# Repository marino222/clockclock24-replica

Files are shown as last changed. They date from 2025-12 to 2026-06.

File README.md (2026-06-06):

# ClockClock 24 Replica

This project is a hardware and software replica of the kinetic art piece "ClockClock 24" by *Humans Since 1982*, inspired by and building upon the work of [Vallasc](https://github.com/Vallasc/clockclock24-replica) with several hardware modifications and improvements. The clock features 24 double-shaft stepper motors arranged in an 8x3 matrix, with motors grouped in sets of three on custom PCBs, of which there are eight in total. Each board is controlled by a Raspberry Pi Pico microcontroller acting as a slave, while all slave boards communicate with a central ESP32 master via the I2C protocol. The ESP32 also provides a web interface for remote control and configuration.

chaos_intro

---

## Table of Contents

1. [Repository Structure](#repository-structure)
2. [Hardware](#hardware)
    1. [Electronics](#electronics)
        1. [Motors](#motors)
        2. [Motor Drivers](#motor-drivers)
        3. [Microcontrollers](#microcontrollers)
        4. [PCB](#pcbs)
        5. [Power Supply](#power-supply)
    2. [Mechanics](#mechanics)
        1. [Clock hands](#clock-hands)
        2. [Fixation brackets](#fixation-brackets)
        3. [Front panel](#front-panel)
    3. [BOM](#bom)
3. [Software](#software)
    1. [Master](#master)
    2. [Slave](#slave)
    3. [Web Interface](#web-interface)
4. [Credits](#credits)

---

## Repository Structure

```
ClockClock 24 Replica/
├── 3D files/
│   ├── final/
│   └── test/
├── docs/
│   ├── datasheets/
│   └── images/
├── firmware/
│   ├── arduino/
│   │   ├── AdvancedBoardTest/
│   │   ├── BoardTest/
|   |   ├── SerialBoardTest/
│   │   └── SpeedoDriveTest/
│   ├── platformio/
│   │   ├── master/
│   │   └── slave/
│   └── README.md
├── pcb/
│   ├── Clock PCB/
│   └── Motor Driver/
└── README.md
```

---

## Hardware

### Electronics

#### Motors
To drive the clock hands, the BKA30D-R5 (equivalent to VID28-05) stepper motors were chosen. They have a total of 4 coils, allowing for two concentric drive shafts which makes them perfect for this application. These motors were originally designed for dashboard applications in the automotive industry. There are a number of other options with concentric shafts, but this one seemed to be most suitable as other similar projects also used it. Furthermore, it is cheaply available (around 4$ on Aliexpress) and draws little current.

<p align="center">
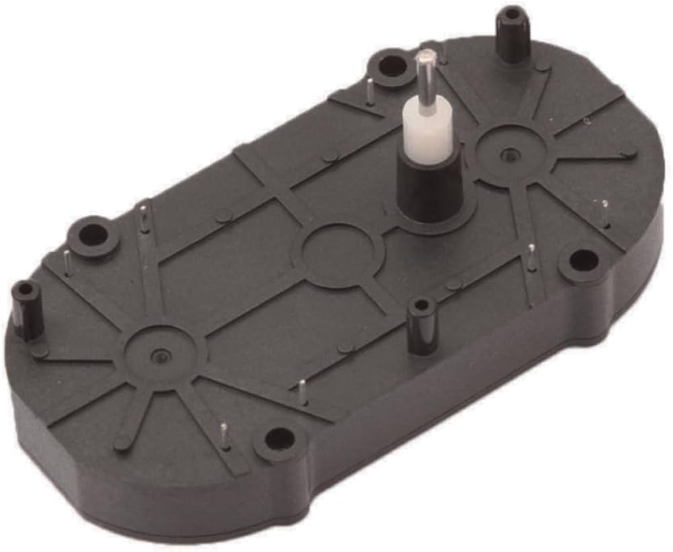
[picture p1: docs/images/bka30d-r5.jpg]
BKA30D-R5 stepper motor
    
    <br><em>BKA30D-R5 stepper motor</em>
</p>

The BKA30D-R5 allows for microstepping up to 1/12 degrees per microstep, which is ideal to achieve smooth movement of the clock hands. See datasheet for more details: [BKA30D-R5 Datasheet](docs/datasheets/BKA30D-xx_datasheet.pdf).

*Note: As standard, this motor comes with mechanical endstops. On Aliexpress there are some vendors that sell it without endstops, otherwise you will need to cut off the endstops yourself.*

---

#### Motor Drivers
The steppers could in theory be driven directly from the microcontroller. However, the GPIO pins are limited and it is usually best practice to use a dedicated motor driver. For this reason, the VID6606 motor driver was chosen. It is specifically designed for the BKA30D-R5 (VID28-05) motor. One VID6606 can drive 4 motors (8 coils) in total. Per motor, it only needs two inputs: `f(SCX)` and `DIR`. As standard, this controller has built-in microstepping, which means with each rising edge of the SCX input the motor will perform one microstep in the direction specified by the DIR input.

The [VID6606 Datasheet](docs/datasheets/VID6606_datasheet.pdf) specifically recommends the use of smoothing capacitors to reduce electrical noise. Therefore, this [Motor-Controller-PCB from Hackaday](https://hackaday.io/project/187630-stepper-driver-for-dashpanel-instruments) was used. I didn't make any changes to it because it was already tested by [doctek](https://hackaday.io/doctek). Thus, it is designed to be used as a breakout board on the custom Clock PCB.

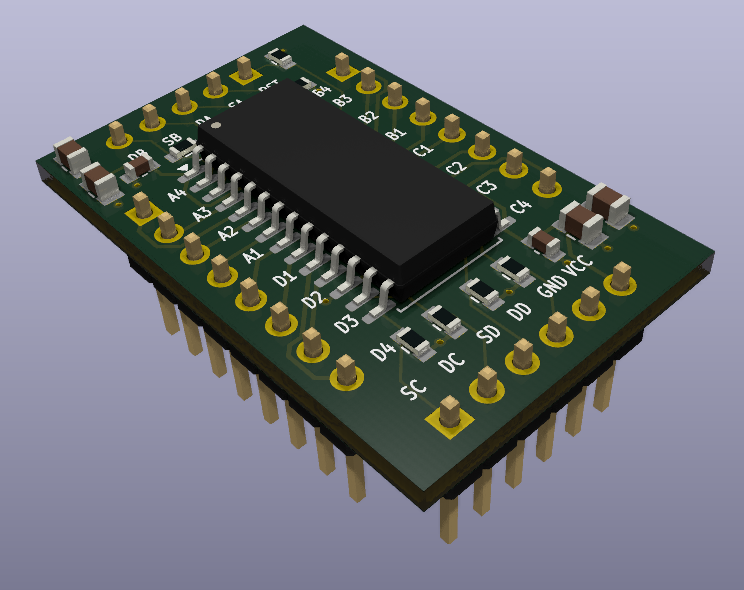
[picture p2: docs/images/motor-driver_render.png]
Rendered Motor Driver PCB

<p align="center"><em>Rendered image of the motor driver PCB</em></p>

During testing, the steppers were quite noisy. I first suspected the motor drivers and tried some alternatives (DRV8834, TMC2208), but that didn't help much, so I stayed with the VID6606. 

The real cause turned out to be mechanical play in the motor shafts. I also noticed the noise only appears at certain speeds, at full speed it mostly goes away. So adjusting the acceleration profile in software might help. For now I decided to leave the mechanical play as-is, since adding a bearing would be quite complex.

---

#### Microcontrollers
An ESP32 was chosen to run the master code, while multiple Raspberry Pi Picos are used as slave controllers. The ESP32 sends all the commands via I2C protocol to the slave boards. The main reason for this choice is that almost the same controllers were used in the reference project ([Vallasc/clockclock24-replica](https://github.com/Vallasc/clockclock24-replica)). Since I want to copy the software as closely as possible, I stuck with the same controllers. They are also widely available for a reasonable price and are easy to work with.

<p align="center">
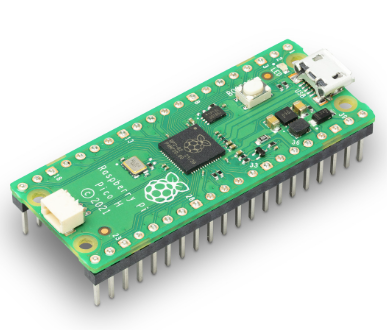
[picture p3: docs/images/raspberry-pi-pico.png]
Raspberry Pi Pico
    
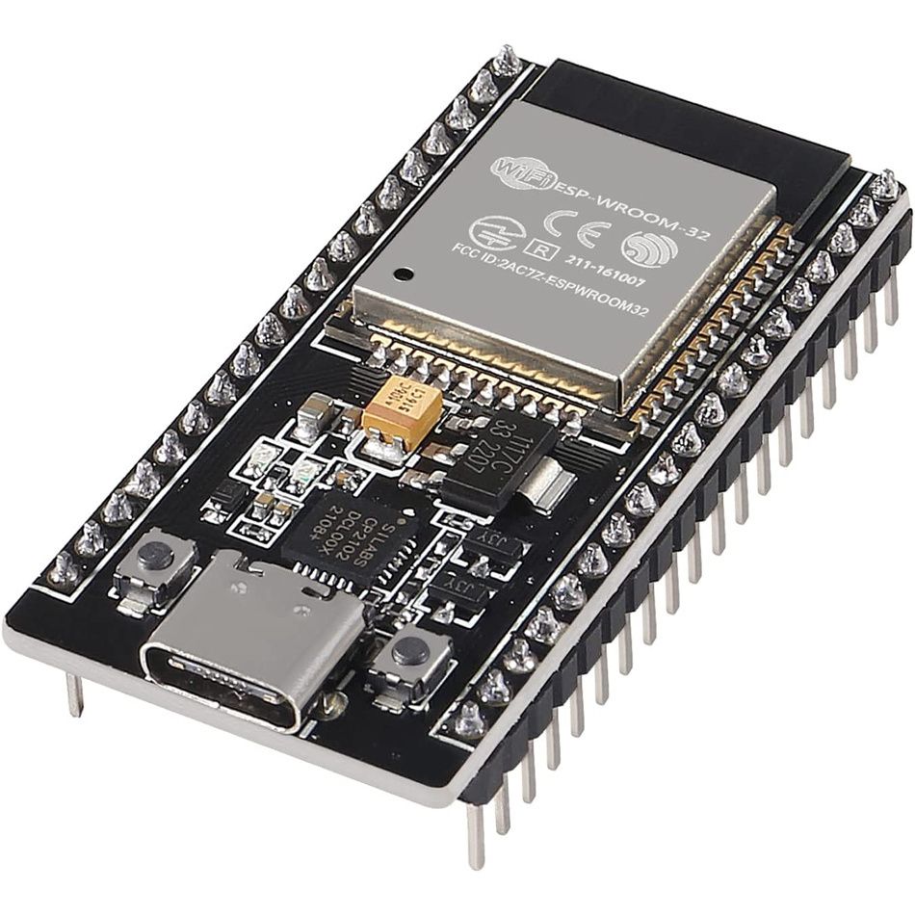
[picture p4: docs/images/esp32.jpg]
ESP32
    
</p>
<p align="center"><em>Raspberry Pi Pico (left) and ESP32 (right)</em></p>

---

#### PCB
For the project, a custom Clock PCB was designed to hold three BKA30D-R5 motors, which is the maximum number of motors that can be driven by one Raspberry Pi Pico regarding available GPIO pins. In total, there are eight of these PCBs, resulting in an 8x3 matrix of 24 motors. Each Clock PCB has two VID6606 motor driver breakout boards, of which one output is unused.

As a design choice, the PCB uses header pins to connect the motor drivers and the microcontroller. This makes it easy to replace components in case they break. While testing, this happened multiple times. Since the motor controllers were directly soldered onto the PCB in the beginning, I ended up throwing away the whole PCB each time a motor driver broke. The header pins solve this problem. As a bonus, the Picos can be switched out easily. This proved useful to quickly run a test program by replacing the "normal" slave controller with a test controller running different firmware.

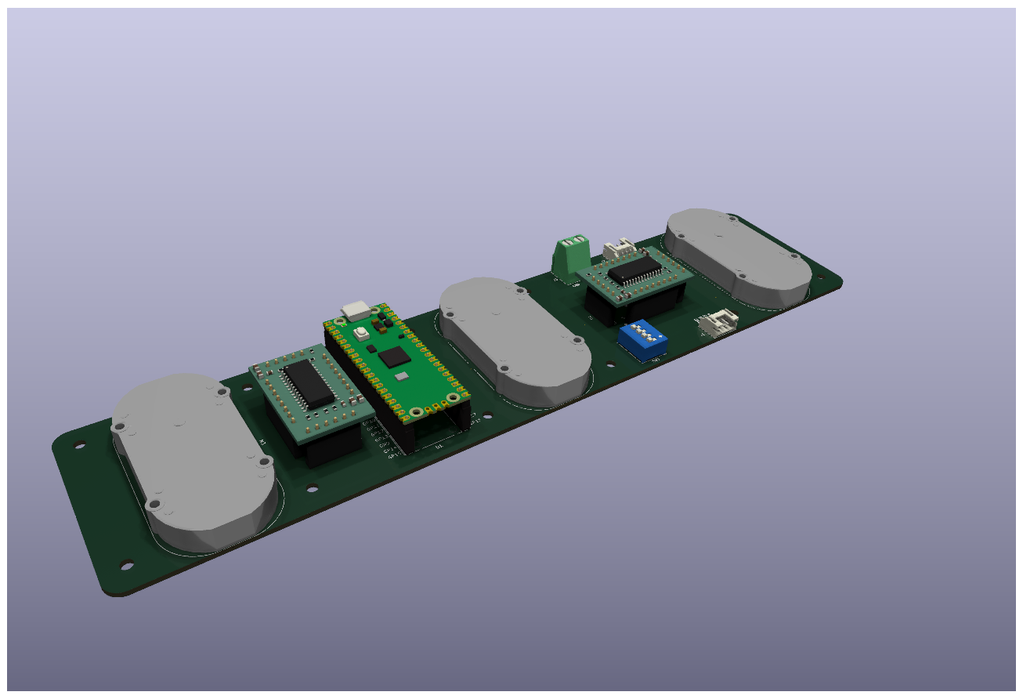
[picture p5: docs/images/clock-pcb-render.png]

<p align="center"><em>Rendered image of the Clock PCB. See PCB directory for more info</em></p>

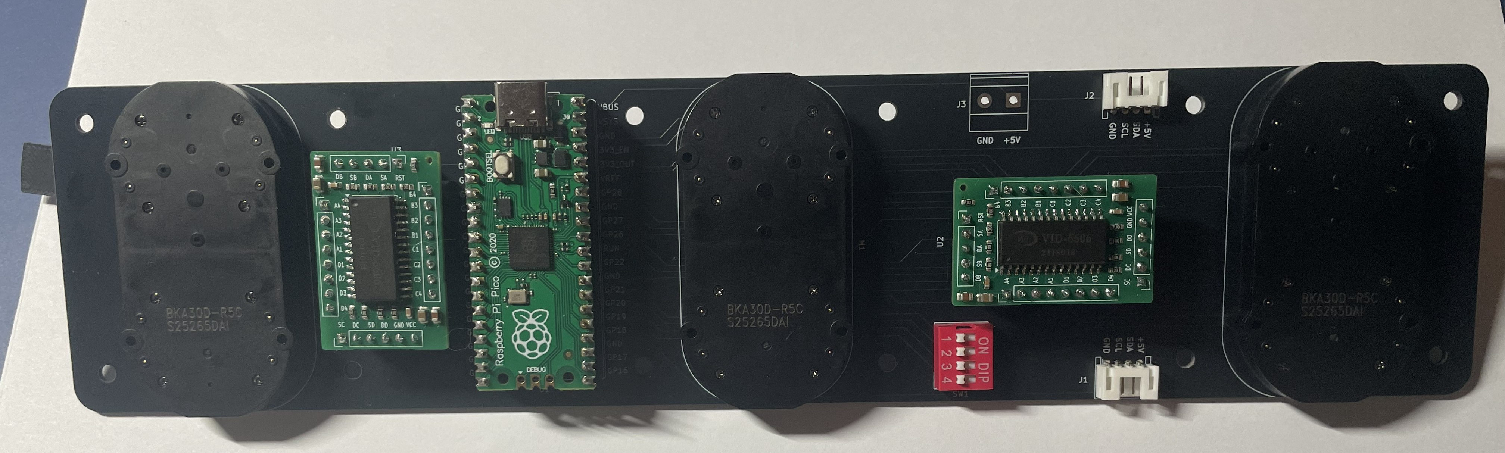
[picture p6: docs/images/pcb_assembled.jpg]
Assembled Clock PCB

<p align="center"><em>Assembled Clock PCB</em></p>

---

#### Power Supply
All the PCBs are connected by a JST-XH 4-pin connector in a daisy chain. Two wires are used for power (5V and ground) and two wires are used for I2C communication (SDA and SCL). In theory, it should be possible to power all eight PCBs from one Raspberry Pi Pico connected to a power supply via USB-C. However, in reality this didnt work (see below).

#### Power Consumption Table

| Device | Normal Current (mA) | Peak Current (mA) | Quantity | Total Normal (mA) | Total Peak (mA) |
|---|---|---|---|---|---|
| Raspberry Pi Pico | 50 | 100 | 8 | 400 | 800 |
| Stepper Motor | 20 | 20 | 24 | 480 | 480 |
| ESP32 | 260 | 700 | 1 | 260 | 700 |
| **Total** | | | | **1140** | **1980** |

This table shows the estimated current draw for each device during normal use and at peak. The totals are for 8 Raspberry Pi Picos, 24 stepper motors, and 1 ESP32.

A Raspberry Pi Pico can provide up to 2 A via the VBUS pin when powered over USB-C, which should be enough even at peak load.

In practice I ran into power problems. When all motors start up at the same time, they draw a lot of current and the Pico's supply couldn't keep up, causing the ESP32 or some Picos to randomly shut down. To fix this, each PCB has an extra 2-pin JST power input. I disconnected the +5V lines on the JST-XH 4-pin connectors (GND and I2C stay connected) and wired the 2-pin terminals with 18 AWG wire and WAGO clamps to a separate supply.

The worst-case current draw is around 4 A, so I chose a 5 V / 6 A (30 W) PSU from [Amazon](https://www.amazon.de/dp/B0FY6691ZL), which gives a 2 A safety margin. It connects via a standard barrel jack that came with the PSU.

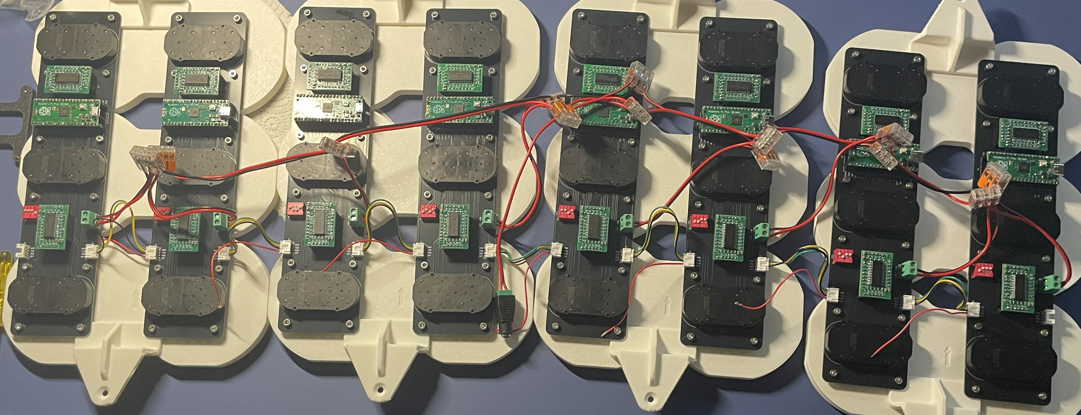
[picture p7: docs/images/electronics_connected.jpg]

<p align="center"><em>Image of the connected PCBs</em></p>

### Mechanics

All mechanical parts are modeled in CAD. See the [3D files README](3D%20files/README.md) for the full assembly and a list of all printable parts.

#### Wooden Frame & Front panel

For the front panel I wanted a clean matte white look. After exploring several options (PVC, painted MDF, Corian), I found [expresszuschnitt.de](https://expresszuschnitt.de/) where you can order custom laser-cut materials. I ordered some samples and went with matte white acrylic (PERSPEX® Frost). The quality is excellent and the finish looks great. The front panel is bonded to the wooden frame with 3M VHB tape.

The frame itself is made from four wooden beams (see [BOM](#bom) for dimensions), connected at the corners by 3D-printed brackets that are screwed onto the beams.

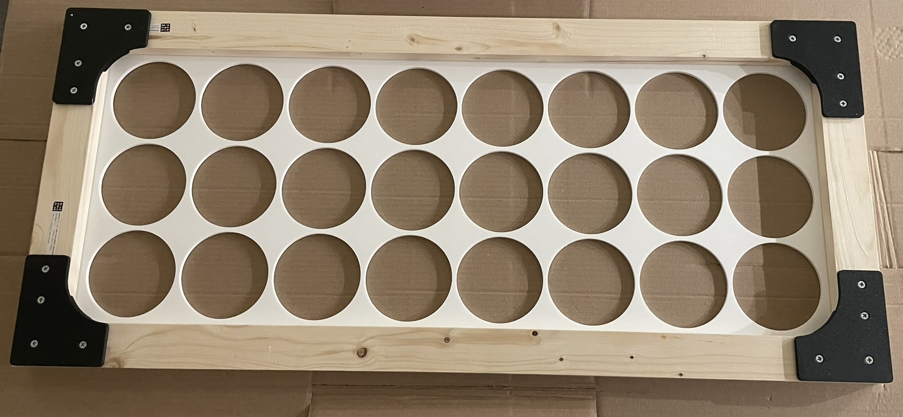
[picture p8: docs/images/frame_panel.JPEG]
Wooden frame and front panel

<p align="center"><em>Wooden frame with acrylic front panel</em></p>

To give the clock a picture-frame look, I added medium oak ledges glued onto the main frame with mitered corners. Cutting accurate miters with basic tools was tricky, but after some sanding and oiling the result looks quite nice.

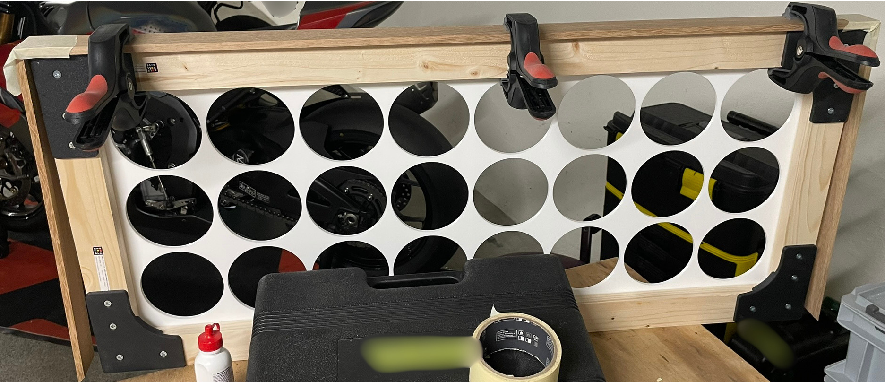
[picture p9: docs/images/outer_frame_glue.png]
Outer frame being glued

<p align="center"><em>Gluing the outer oak frame</em></p>

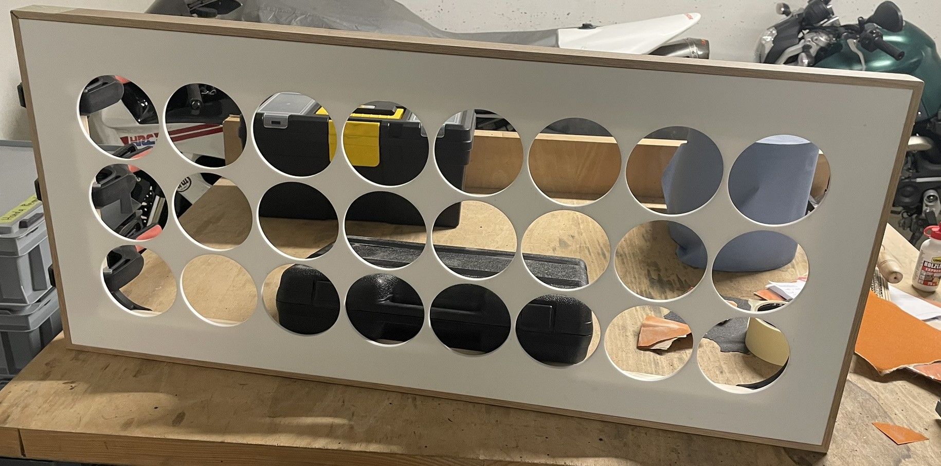
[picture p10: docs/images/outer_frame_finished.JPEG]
Finished outer frame

<p align="center"><em>Finished outer frame</em></p>

---

#### 2×3 Clock Arrays

The motors are grouped into 2×3 arrays. Each array consists of two PCBs connected by PCB mounts. Screw spacers raise the PCBs to the correct depth so the clock hands sit at the right position on the front. Everything is held together with M3 hex screws and threaded inserts.

<p align="center">
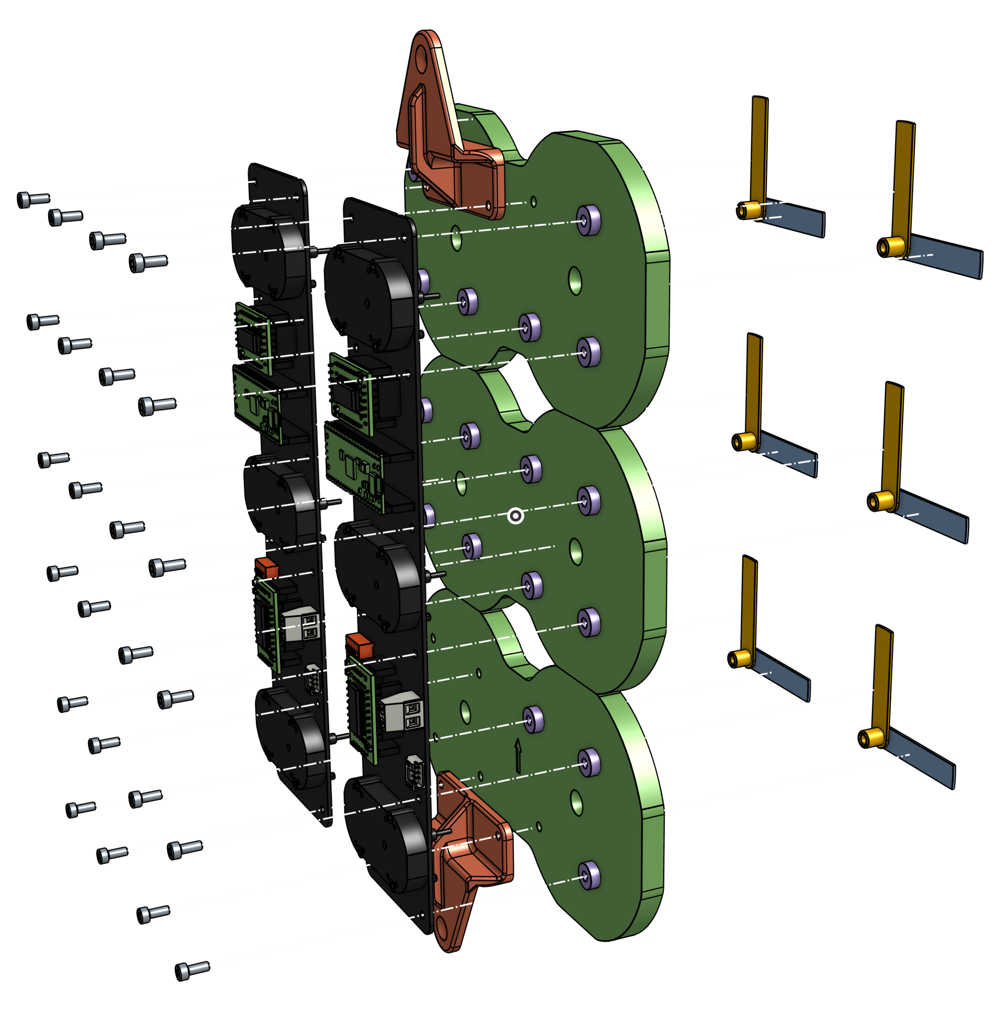
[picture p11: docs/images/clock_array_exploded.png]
2×3 clock array exploded view
    
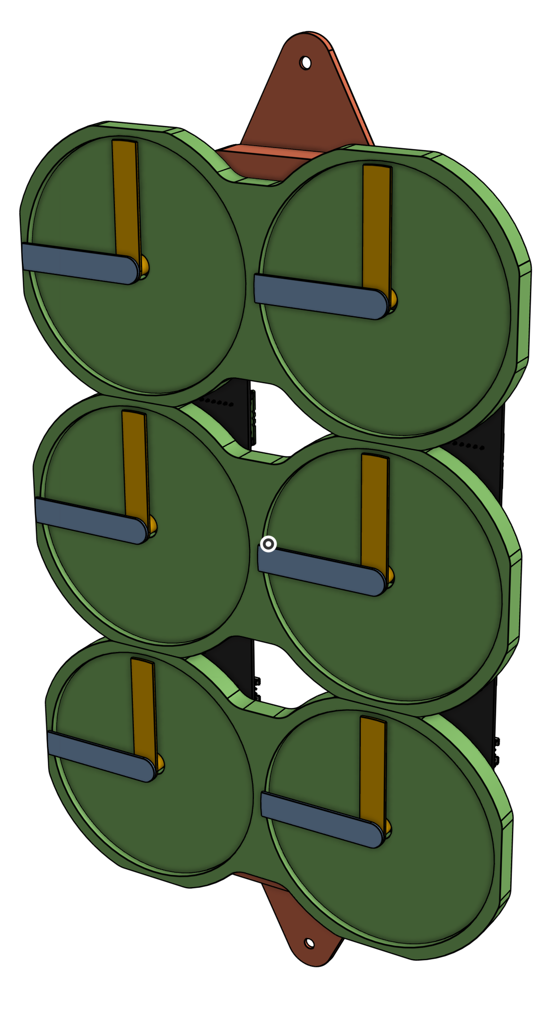
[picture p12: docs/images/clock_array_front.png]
2×3 clock array front view
    
</p>
<p align="center"><em>Exploded view (left) and front view (right) of a 2×3 clock array</em></p>

The arrays are aligned with the holes in the front panel using the [`mounting_aid.stl`](3D%20files/README.md) and then screwed to the wooden frame. The PSU barrel jack is clamped to the bottom of the frame with a 3D-printed bracket. A small cutout in the outer frame lets the power cable pass through.

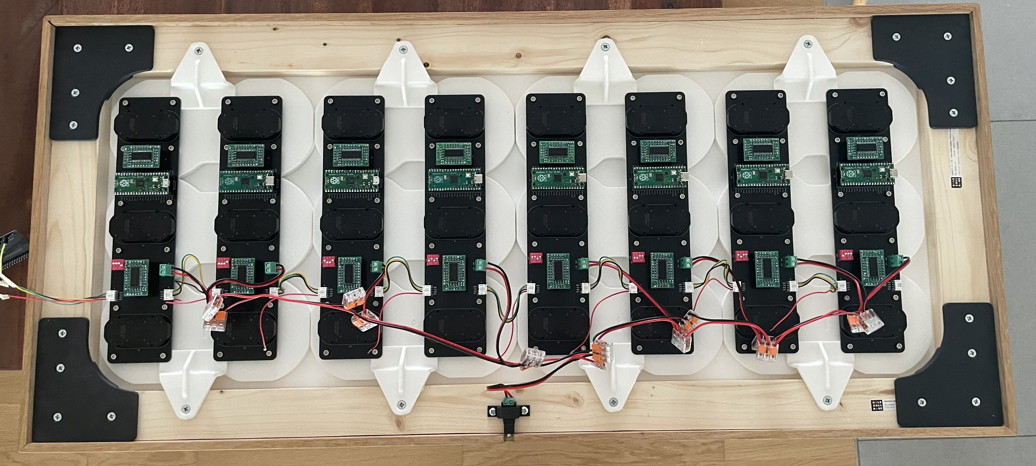
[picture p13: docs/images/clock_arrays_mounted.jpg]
Clock arrays mounted to the frame

<p align="center"><em>Clock arrays mounted to the frame</em></p>

---

#### Clamps

After mounting everything, I noticed a visible air gap between the 3D-printed PCB mounts and the front plate. This comes from slightly bent 3D-printed parts. The front panel also has quite a bit of flex.
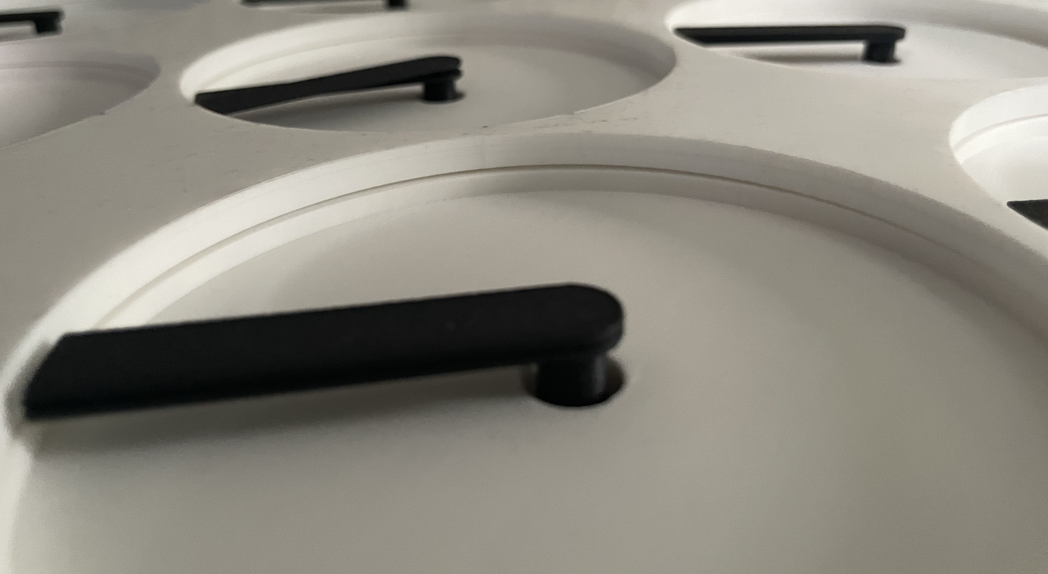
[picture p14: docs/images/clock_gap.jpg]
Gap between clock arrays and front panel

<p align="center"><em>Gap between clock arrays and front panel</em></p>

To fix this, I designed a clamp to press the PCB holders onto the front plate. I tried different solutions, but none gave satisfying results. In the end, I settled on 3D-printed clamps that are screwed onto the main frame and use a spring section to press the PCB holders against the front plate.

Section view of clamps
<p align="center"><em>Section view of clamps</em></p>

Because of build-volume restrictions on my 3D printer, each clamp consists of multiple parts that are screwed together. As a result, and because the 3D-printed springs are quite strong, the clamp bends slightly. This can be seen in the image below. The bending causes the clamp to sit slightly higher than the outer frame. As a result, when the clock is mounted on a wall, the outer frame is not fully flush because the clamps push the clock outward. I decided to treat this as a design feature: it protects the rest of the clock, and the gap between the frame and the wall allows a bit of airflow, which helps cool the microcontrollers.

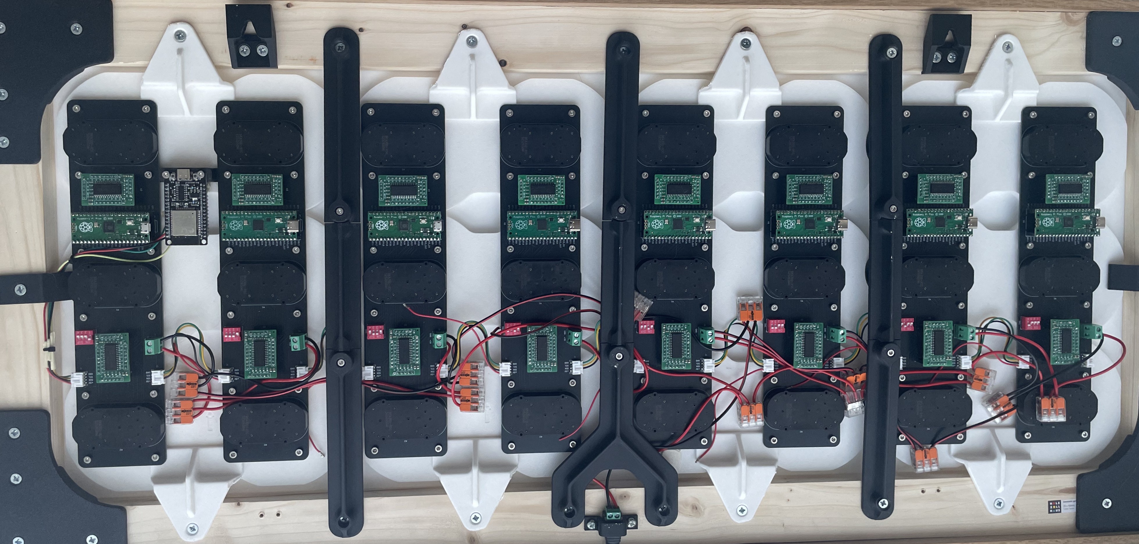
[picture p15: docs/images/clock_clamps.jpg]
Assembled clock with clamps

<p align="center"><em>Assembled clock with clamps</em></p>

---
### BOM

| Component | Description | Quantity | Source | Link |
|---|---|---|---|---|
| Clock PCB | Custom PCB holding 3 motors and a Raspberry Pi Pico. See PCB directory for the electronic BOM | 8 | JLCPCB, parts from AliExpress | [PCB README](pcb/Clock%20PCB/README.md) |
| PCB Mount (3D printed) | Mounts two PCBs together into one 2×3 array. 3 pieces per array | 9 | Self-printed | [3D files README](3D%20files/README.md) |
| PCB Mount Bottom (3D printed) | Same as PCB Mount but with corrected hole positions for the bottom PCB | 3 | Self-printed | [3D files README](3D%20files/README.md) |
| Mounting Bracket (3D printed) | Connects a 2×3 clock array to the wooden frame | 6 | Self-printed | [3D files README](3D%20files/README.md) |
| PSU Bracket (3D printed) | Clamps the PSU barrel jack to the wooden frame | 1 | Self-printed | [3D files README](3D%20files/README.md) |
| Frame Connector (3D printed) | Connects the outer frame corners. Parts are mirrored for each corner | 4 | Self-printed | [3D files README](3D%20files/README.md) |
| Screw Spacer (3D printed) | Raises PCBs slightly off the mounting brackets | 80 | Self-printed | [3D files README](3D%20files/README.md) |
| Lower Hand (3D printed) | Hour clock hand | 24 | Self-printed | [3D files README](3D%20files/README.md) |
| Upper Hand (3D printed) | Minute clock hand | 24 | Self-printed | [3D files README](3D%20files/README.md) |
| Wall Mount (3D printed) | Wall mounting part | 2 | Self-printed | [3D files README](3D%20files/README.md) |
| Outer Clamp (3D printed) | Outer clamp part | 5 | Self-printed | [3D files README](3D%20files/README.md) |
| Middle Clamp (3D printed) | Middle clamp part | 3 | Self-printed | [3D files README](3D%20files/README.md) |
| Y-Clamp (3D printed) | Y-clamp part | 1 | Self-printed | [3D files README](3D%20files/README.md) |
| Leaf Spring (3D printed) | Spring element used in the clamp assembly | 9 | Self-printed | [3D files README](3D%20files/README.md) |
| Edge Clamp (3D printed) | Edge clamp part for the right and left sides | 2 | Self-printed | [3D files README](3D%20files/README.md) |
| ESP32 mount (3D printed) | Mounting part for the ESP32 microcontroller | 1 | Self-printed | [3D files README](3D%20files/README.md) |
| Acrylic Front Panel | PERSPEX® Frost matte white acrylic, 900×400×5 mm | 1 | Imported from Germany | [expresszuschnitt.de](https://expresszuschnitt.de/) |
| Main Frame Long | 20×45×900 mm wood beam | 2 | Hardware store | [Jumbo](https://www.jumbo.ch/de/bauen-renovieren/holz/leisten-staebe/rechteckleisten/oecoplan-dachlatte-gehobelt-20-x-45mm--1m/p/4974449) |
| Main Frame Short | 20×45×400 mm wood beam | 2 | Hardware store | [Jumbo](https://www.jumbo.ch/de/bauen-renovieren/holz/leisten-staebe/rechteckleisten/oecoplan-dachlatte-gehobelt-20-x-45mm--1m/p/4974449) |
| Outer Frame Long | 8×40×920 mm oak ledge | 2 | Hardware store | [Jumbo](https://www.jumbo.ch/de/bauen-renovieren/holz/leisten-staebe/rechteckleisten/rechteckleiste-eiche-8x40-mm-1-m/p/4974225) |
| Outer Frame Short | 8×40×420 mm oak ledge | 2 | Hardware store | [Jumbo](https://www.jumbo.ch/de/bauen-renovieren/holz/leisten-staebe/rechteckleisten/rechteckleiste-eiche-8x40-mm-1-m/p/4974225) |
| Power Supply | 5 V / 6 A (30 W) PSU | 1 | Amazon | [Amazon](https://www.amazon.de/dp/B0FY6691ZL) |
| Power Wire | 18 AWG | ~3 m | AliExpress | |
| WAGO Clamps | Model 221-413 (3-conductor) | 14 | AliExpress | |
| 3M VHB Tape | 19 mm width | ~1 m | Hardware store | [3M Switzerland](https://www.3mschweiz.ch/3M/de_CH/p/c/klebebander/b/vhb/) |
| Countersunk Wood Screw | 4×16 mm | 24 | Hardware store | [Jumbo](https://www.jumbo.ch/de/maschinen-werkstatt/kleineisenwaren/schrauben/holzschrauben/ayce-senkkopf-universalholzschraube--4--16-mm/p/6932501) |
| Hex Screw | M3×8 mm | 96 | AliExpress | |
| Threaded Insert | M3×4×4 mm (for 3D-printed parts) | 96 | AliExpress | |

---

## Software

### Master

The master firmware runs on an ESP32 microcontroller and acts as the central brain of the clock. Its main responsibilities include:

- **Time Synchronization**: Automatically connects to WiFi to retrieve the current time, ensuring the clock is always accurate and handles time zones and daylight saving time seamlessly.
- **Clock Logic**: Orchestrates the movements of all clock hands, deciding exactly what positions they need to be in to display the time or play animations.
- **Communication**: Sends synchronized instructions to all eight slave boards so the 24 motors move perfectly together.
- **Web Server**: Hosts a web interface that allows you to configure and control the clock from any device.

The master code is built using PlatformIO with the Arduino framework.

### Slave

The slave firmware runs on each of the eight Raspberry Pi Pico microcontrollers, with each board responsible for controlling three BKA30D-R5 stepper motors (six individual clock hands). Key features include:

- **I2C Communication**: Listens for commands from the ESP32 master via I2C protocol
- **Motor Control**: Uses the AccelStepper library to provide smooth, accelerated motor movements with precise positioning
- **Automatic Addressing**: Determines its I2C address automatically based on DIP switch configuration (see below)

Each slave board operates independently once it receives position commands from the master, managing the acceleration profiles and step timing for its three motors in parallel.

Each slave board (Raspberry Pi Pico) determines its I2C address automatically based on four DIP switch pins (ADDR_1 through ADDR_4) defined in [`board_config.h`](firmware/platformio/slave/include/board_config.h). The address is calculated in [`board.cpp`](firmware/platformio/slave/src/board.cpp) by reading the state of these pins, which use INPUT_PULLUP logic. When a DIP switch is ON (connected to ground), it represents a binary 1. When OFF (open/floating), it represents a binary 0.

The master controller sends commands to each board sequentially as seen in [`clock_manger.cpp`](firmware/platformio/master/src/clock_manger.cpp), where I2C address 15 corresponds to the rightmost board. The first address is 0x08, because in the I2C protocol 0x01 to 0x07 are reserved.

#### Board Address Configuration (Left to Right)

| I2C Address | Binary | DIP 1 | DIP 2 | DIP 3 | DIP 4|
|---|---|---|---|---|---|
| 8  | 1000 | 1 | 0 | 0 | 0 |
| 9  | 1001 | 1 | 0 | 0 | 1 |
| 10 | 1010 | 1 | 0 | 1 | 0 |
| 11 | 1011 | 1 | 0 | 1 | 1 |
| 12 | 1100 | 1 | 1 | 0 | 0 |
| 13 | 1101 | 1 | 1 | 0 | 1 |
| 14 | 1110 | 1 | 1 | 1 | 0 |
| 15 | 1111 | 1 | 1 | 1 | 1 |

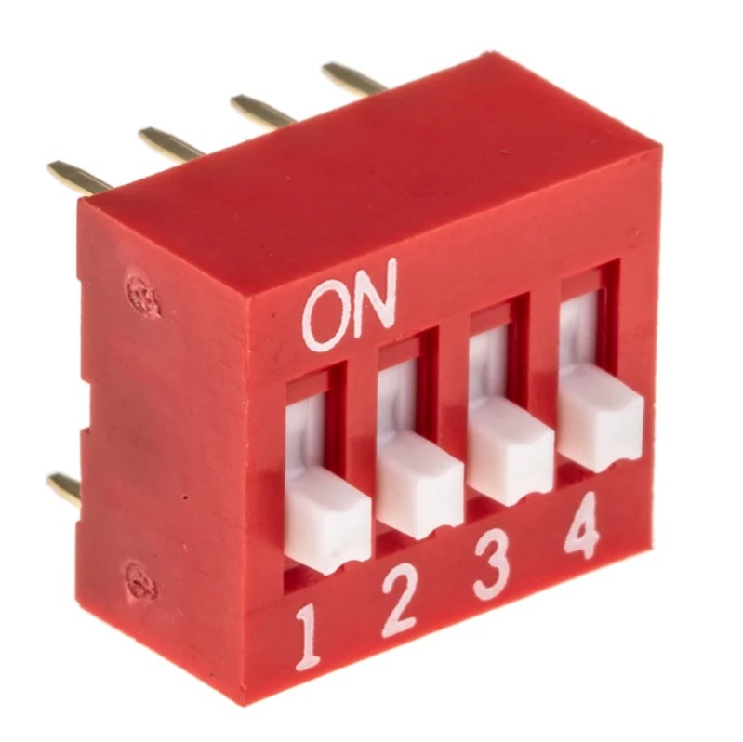
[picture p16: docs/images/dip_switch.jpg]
DIP Switch


### Web Interface

The web interface is hosted directly on the ESP32 and provides an intuitive control panel for the ClockClock 24. To access it, simply connect to the same WiFi network as the ESP32 and navigate to its IP address in your browser. 

The UI provides the following features:
- **Live Preview**: View a real-time digital representation of what the physical clock is currently displaying.
- **Mode & Animation Selection**: Easily switch between the normal time display, various choreographies, or run test animations.
- **Sleep Time Configuration**: Define specific days and hours when the clock should stop moving to save power and reduce noise.
- **Wireless Configuration**: Seamlessly switch between the clock's own Hotspot mode or connect it to your home WiFi network.
- **Firmware Update**: Perform Over-The-Air (OTA) firmware updates directly from your browser.

The web interface is built using standard HTML, CSS, and JavaScript. Because the ESP32 has limited storage, a custom Node.js script is used to compress the web files. Before building the firmware, running `npm run minimize` minifies the UI files and converts them into a single, optimized C++ header file, which is then flashed onto the microcontroller.

For more technical details about the firmware, see the [firmware README](firmware/README.md).

### Clock Modes

The clock can operate in three distinct modes, which can be selected via the web interface:
- **OFF**: All clock hands move to a resting position (pointing straight down) and remain stationary.
- **LAZY**: A minimalist mode where the clock hands take the shortest, most direct path to the new time every minute, without any complex choreographies.
- **ANIMATED**: Every minute, the clock performs a choreography before settling on the new time. You can choose a specific animation or use the **Cycle** mode.

#### Cycle Mode & Randomness
When the **Cycle** animation is selected, the clock rotates through the available choreographies instead of playing the same one every minute. You have two options for how it cycles:
- **SEQ (Sequential)**: Plays the animations in a fixed order, cycling to the next one every minute.
- **RAND (Random)**: Plays a "random" animation each minute. Interestingly, this randomness is deterministic and based on the current time (a hash of the current minute of the day). This means the clock will always play the exact same animation, as the Web Interface.

### Animations

| Description | Animation |
| --- | --- |
| Chaos | chaos |
| Waves | waves |
| Circle | circle |
| Spiral | spiral |
| Loom | loom |
| Star | star |

## Credits

### Design — Humans Since 1982

**ClockClock 24 is an original kinetic art piece created by [Humans Since 1982](https://www.humanssince1982.com/).** All design rights, intellectual property, and artistic authorship of the ClockClock concept belong exclusively to them. This project is a non-commercial personal replica built out of admiration for their work. I make no claim to the design, the concept, or any related intellectual property.u are considering a similar project, please be aware of this and respect their rights.

---

### Reference Implementation — Vallasc

The firmware and PCB design of this project are largely based on the work of [Vallasc](https://github.com/Vallasc/clockclock24-replica). His open-source replica served as the primary reference for the software architecture, I2C communication protocol, clock logic, and overall system design. Without his work this project would have taken significantly longer to build.

---

### Motor Driver PCB — doctek

The motor driver breakout board design is taken from the [Stepper Driver for Dashpanel Instruments](https://hackaday.io/project/187630-stepper-driver-for-dashpanel-instruments) project by [doctek](https://hackaday.io/doctek) on Hackaday.io. The board was used without modifications. The `SpeedoDriveTest.ino` test sketch is also taken from that project.

---

### This Project

This repository is released under the [GNU General Public License v3.0](LICENSE). You are free to use, modify, and distribute it under the same terms, but **the design concept of ClockClock 24 remains the exclusive property of Humans Since 1982** and this license does not grant any rights to it.

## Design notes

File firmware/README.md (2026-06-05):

# Firmware

This directory contains the source code for the project, targeting both the Raspberry Pi Pico and the ESP32 microcontrollers.

## Overview

- **Master**: Runs on the ESP32.
- **Slave**: Runs on the Raspberry Pi Picos.

The firmware is largely based on the code in [Vallasc's clockclock24-replica repository](https://github.com/Vallasc/clockclock24-replica). Therefore, all credits go to [Vallasc](https://github.com/Vallasc).

## Architecture Details

### Master (ESP32)
The Master acts as the central coordinator for the entire clock and handles the following high-level tasks:
- **Web Server & UI**: Hosts an asynchronous web server that serves the control panel UI. The ESP32 also acts as a DNS server when in Hotspot (AP) mode to redirect users to the interface.
- **Timekeeping**: Connects to the internet via WiFi to synchronize time using an NTP client. It manages timezones and daylight saving time adjustments automatically.
- **Clock Logic & Animations**: Contains the logic defining the target angles for every single clock hand to display numbers, custom patterns, or complex choreography.
- **I2C Master**: The ESP32 sequentially communicates with the 8 slave boards via I2C, sending them their new target motor positions so that all 48 hands move in unison.

### Slave (Raspberry Pi Pico)
The ClockClock 24 uses 8 Slave boards. Each Pico manages 3 custom stepper motor modules, each equipped with a double-shaft stepper motor (totaling 6 hands per slave).
- **I2C Slave**: Listens on its specific I2C address (0x08 to 0x0F) for position commands from the Master. The I2C address is dynamically set at boot based on the board's physical DIP switches.
- **Motor Control**: Uses the `AccelStepper` library to concurrently drive the 6 connected hands. The slave independently manages the acceleration, deceleration, and step timing for each motor, freeing the Master from real-time motor control.

### Web UI Build Process
To optimize flash storage usage and maximize loading speeds on the ESP32, the Web UI is not stored as distinct files on a filesystem (like SPIFFS/LittleFS).
Instead, a custom Node.js script (`platformio/master/web/minimize.js`) is used to bundle the interface. By running `npm run minimize` in the `web` directory, the script:
1. Inlines all external CSS and JavaScript directly into the HTML file.
2. Minifies the resulting code by stripping comments and whitespace.
3. Generates C++ header files (`web_page.h` and `ota_page.h`) containing the fully optimized UI as static C string macros.

These headers are then compiled directly into the ESP32 firmware, allowing the web server to serve them directly from memory.

## Project Structure

### PlatformIO Projects
The main firmware is developed using PlatformIO and contains only the final firmware.

- **`master/`**: Source code for the ESP32 (Master). Includes the web UI source code inside the `master/web/` directory.
- **`slave/`**: Source code for the Raspberry Pi Picos (Slaves).

### Arduino Scripts
- **`arduino/`**: Contains Arduino scripts used for testing purposes. These scripts were developed and tested using the Arduino IDE. Arduino test scripts are faster and easier to set up, avoiding the hassle of configuring PlatformIO projects for simple tests. The Arduino IDE can be used for these scripts because the PlatformIO project uses the same Arduino framework, ensuring compatibility.
- For detailed explanations about the Arduino test scripts, refer to the [Arduino README](arduino/README.md).

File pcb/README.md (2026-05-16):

# PCB Design Files

This folder contains the PCB design files for the Clock PCB and a dedicated PCB for the Stepper Motor Controller. Below is an overview of the designs, modifications, and acknowledgments.

## Overview

### Clock PCB
The Clock PCB is based on the design by [Vallasc](https://github.com/Vallasc) from the [clockclock24-replica repository](https://github.com/Vallasc/clockclock24-replica). The original design was a great starting point, but I made several changes to make it work better and be easier to use.

### Motor Controller PCB
A separate Motor Controller PCB was developed to address challenges encountered during testing and assembly. This design is inspired by the project [Stepper Driver for Dashpanel Instruments](https://hackaday.io/project/187630-stepper-driver-for-dashpanel-instruments) by [Doctek](https://hackaday.io/doctek), found on Hackaday.

## Key Modifications

1. **Separate Motor Controller PCB**
   - The original design integrated the VID6606 controller chips directly onto the Clock PCB. However, soldering these chips proved difficult, resulting in damaged boards during assembly.
   - To resolve this, the Motor Controller was redesigned as a separate PCB with header pins, enabling easy replacement of both the Motor Controller and the Raspberry Pi Pico without the need for desoldering.

2. **Enhanced Motor Controller Design**
   - The Motor Controller PCB now includes all the capacitors and resistors recommended in the official datasheet for the BKA30D-R5 stepper motors, ensuring smoother motor operation.
   - The original design by [Vallasc](https://github.com/Vallasc) omitted decoupling capacitors, which have been added to the new Motor Controller PCB for improved performance.
   - For further details, refer to the [BKA30D-R5 Datasheet](../docs/datasheets/BKA30D-xx_datasheet.pdf) and [VID6606 Datasheet](../docs/datasheets/VID6606_datasheet.pdf).

3. **Removed ESP32 Mounting Positions**
   - The mounting positions for the ESP32 were removed to create space for the Motor Drivers.
   - The main controller is now screwed in place (see [3D files README](3D%20files/README.md)) and connected via JST Pins.

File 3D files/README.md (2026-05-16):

# 3D Models for ClockClock 24 Replica

This directory contains all 3D models used in the project. They are split into parts used in the final build and parts used during testing or as assembly aids. All models and assemblies are also available on OnShape:

- [Final clock assembly](https://cad.onshape.com/documents/a12d0058dc8f8a8e500f6aec/w/9550b1995dbe2a83d5e85df4/e/b2a42626349ffc4887ecd531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)
- [Testing models](https://cad.onshape.com/documents/4a68624e57a3036aa9611f7d/w/db09c1e86378c64516826126/e/82d90400d78a886373dde4d7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)

The STL files in this directory are ready to print. You can also edit the models on OnShape and export them yourself. Note that some parts of the build are not 3D-printed. See the CAD assemblies for the full picture.

All parts were printed on a BambuLab P1S using [Polymaker PolyTerra™ PLA Cotton White](https://polymaker.com/product/polyterra-pla/) to get the purest white possible.

## Final Models

| File | Description |
|---|---|
| `lower_hand.stl` | Hour clock hand |
| `mounting_aid.stl` | Alignment tool for positioning the mounting bracket on the front panel |
| `mounting_bracket.stl` | Connects a 2×3 motor array to the wooden frame |
| `pcb_mount.stl` | PCB mount with a center hole and indentation for the clock hands. Three of these connect two PCBs into a 2×3 array |
| `pcb_mount_bottom.stl` | Same as `pcb_mount.stl` but with corrected hole positions to compensate for a placement mistake in the PCB design (the PCB itself was never updated) |
| `psu_bracket.stl` | Clamps the PSU barrel jack to the wooden frame |
| `screw_spacer.stl` | Raises the PCBs slightly off the mounting brackets |
| `upper_hand.stl` | Minute clock hand |
| `standing_bracket.stl` | Add stands for a testing prototype (see video below) |
| `distance_bracket.stl` | Connect PCBs to create a testing prototype (see video below) |
| `clamp_spring.stl` | Leaf spring element for the clamp assembly |
| `edge_clamp.stl` | Edge clamp for the right and left sides |
| `middle_clamp.stl` | Middle clamp for the central mounting position |
| `outer_clamp.stl` | Outer clamp for mounting positions near the frame edges |
| `wall_mount.stl` | Wall mounting part |
| `y_clamp.stl` | Y-clamp part used in the clamp assembly |
| `esp32_mount.stl` | Part to mount the ESP32 main controller |

Testing prototype
<p align="center"><em>Testing prototype in action</em></p>

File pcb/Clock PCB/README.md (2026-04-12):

# Clock PCB — Main Board for ClockClock 24 Replica

This folder contains the design files, manufacturing resources, and assembly instructions for the Clock PCB used in the ClockClock 24 Replica project. The Clock PCB hosts three stepper motors, a Raspberry Pi Pico microcontroller, and connectors for two Motor Driver modules.

---

## Folder Contents

- **KiCad Design Files:** Schematic and layout for the Clock PCB.
- **Manufacturing Folder:**
  - Gerber files (ZIP) for PCB fabrication

---

## Manufacturing

1. **PCB Fabrication:**
   - Order the PCB from [JLCPCB](https://jlcpcb.com/) or a similar service.
   - Upload the Gerber ZIP file from the `Manufacturing` folder during the order process.

3. **Manual Assembly:**
    - Solder all the components manually

---

## Bill of Materials (BOM)

This BOM lists only the components that need to be soldered onto the Clock PCB. The full BOM for the final assembly is provided in [the main project README](../../README.md).

| Quantity | Reference | Value | Footprint | Description |
|---|---|---|---|---|
| 3 | M1, M2, M3 | BKA30D-R5 | - | Stepper Motor |
| 2 | J1, J2 | JST-PH-4pin | P2.0mm | 4-pin JST PH, 90° angle |
| 2 | - | 20 pin female | P2.54mm |  20 Pin socket |
| 2 | - | 6 pin female header | P2.54mm | 6 Pin socket |
| 1 | - | 5 pin female header | P2.54mm | 5 Pin socket |
| 1 | - | 8 pin female header | P2.54mm | 8Pin socket |
| 1 | SW1 | 4 bit | P2.54mm | 4-bit DIP switch |
| 1 | J3 (optional)  | Power connector | P5.08mm | Optional power connector  |

---

## Images

### Assembled Clock PCB Example
<p align="center">
  Assembled Clock PCB
  <br><em>Assembled Clock PCB</em>
</p>

### PCB Schematics
<p align="center">
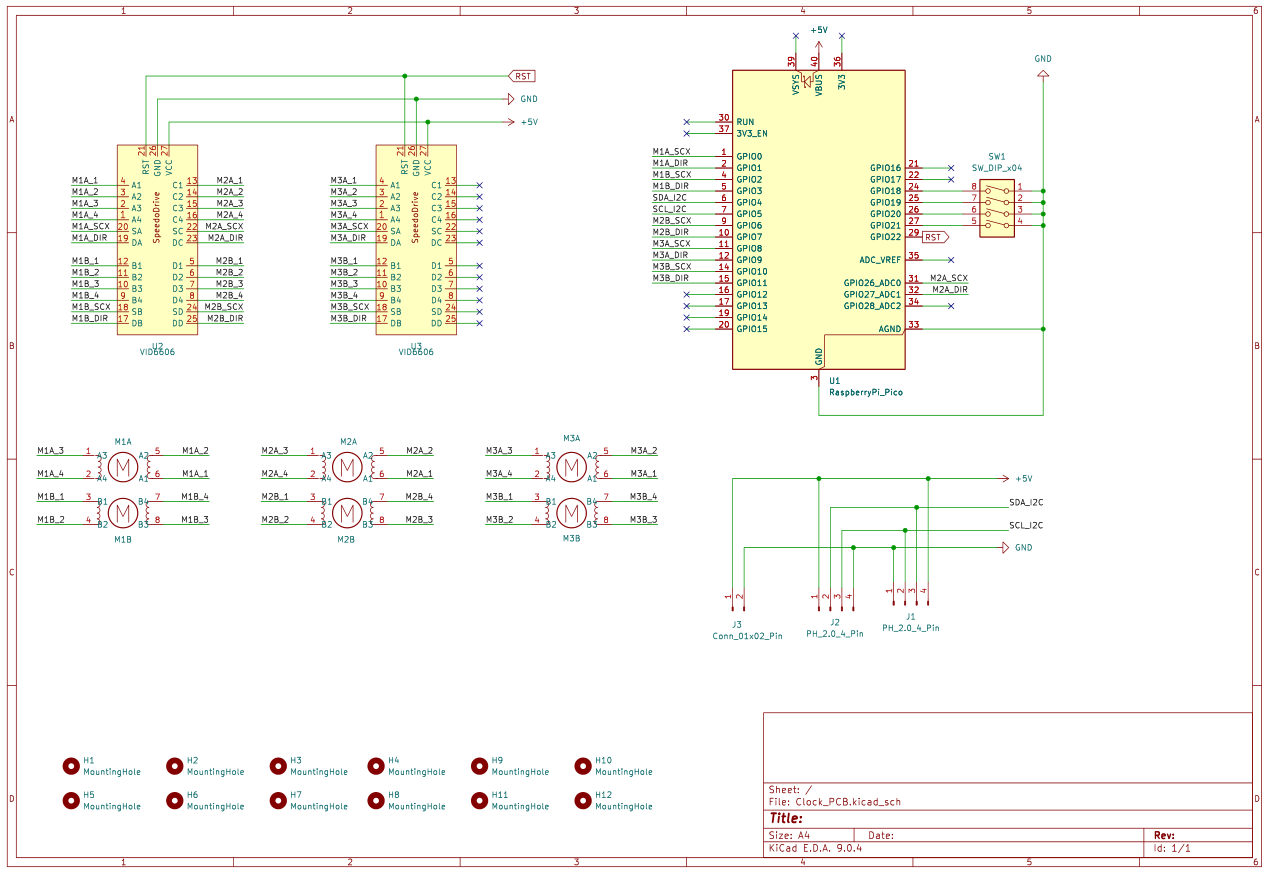
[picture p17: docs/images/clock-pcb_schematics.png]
Clock PCB Schematic
  
  <br><em>Clock PCB Schematic</em>
</p>

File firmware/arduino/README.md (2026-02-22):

# Arduino Test Scripts

This folder contains three Arduino sketches used for testing the ClockClock 24 Replica hardware.

## 1. SpeedoDriveTest

**Purpose:**
This is a basic test script to verify the operation of a single stepper motor driver (specifically designed for the Speedo stepper motors used in this project). It is useful for testing the custom motor driver PCB before assembling the full clock board.

**Origin:**
This script was taken from a project on [Hackaday.io](https://hackaday.io/project/187630-stepper-driver-for-dashpanel-instruments).

**Functionality:**
- Initializes the motor driver.
- Moves the motor to a "zero" position.
- Continuously moves the motor between two positions (3000 and 100) to verify movement and driver control.

**Usage:**
1. Connect your motor driver to the Arduino/Microcontroller as follows:
   - **Enable Pin:** GPIO 20
   - **Direction Pin:** GPIO 6
   - **Step Pin:** GPIO 7
   - **Power:** Connect 5V and GND appropriately.
2. Upload the `SpeedoDriveTest.ino` sketch.
3. The motor should start moving back and forth.

**Test Setup:**
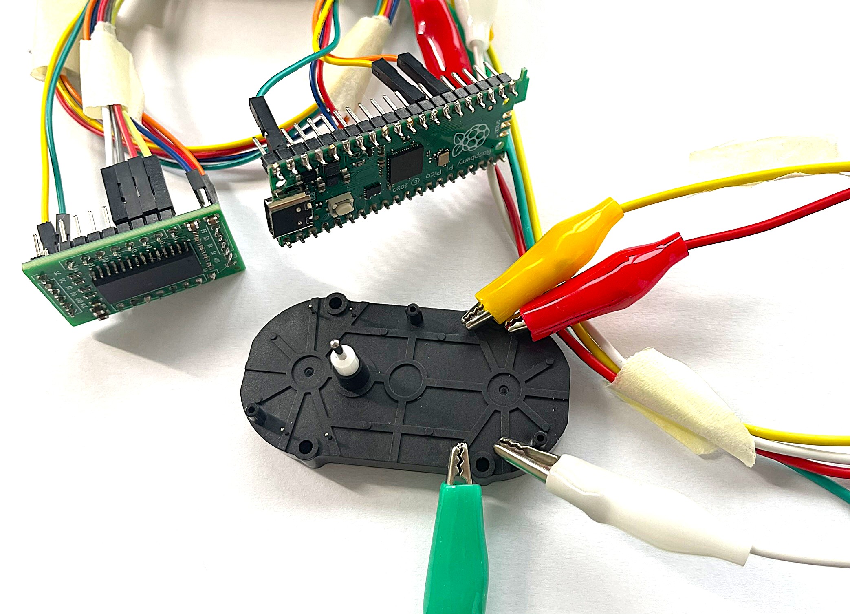
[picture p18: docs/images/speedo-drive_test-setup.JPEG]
Test Setup


## 2. BoardTest

**Purpose:**
This script is designed to test the fully assembled main PCB containing 6 motor drivers. It verifies that all motor drivers are functioning and wired correctly to the microcontroller.

**Functionality:**
- Sequentially activates each of the 6 motors (A through F).
- Rotates Motor A forward one full rotation, then backward one full rotation.
- Repeats this process for Motor B, C, D, E, and F.
- Loops continuously.

**Usage:**
1. Flash the `BoardTest.ino` sketch to the main controller board.
2. Power up the board.
3. Observe the motors. They should move one by one in order (A -> F).

---

## 3. AdvancedBoardTest (Board Bit Testing)

**Purpose:**
This is a more advanced test utility that allows you to select and test a specific motor using a 4-bit binary address. This is useful for debugging specific motor channels without waiting for the sequential loop of the standard `BoardTest`.

**Functionality:**
- Reads a 4-bit address from GPIO pins 18, 19, 20, and 21.
- Activates only the motor corresponding to the set address.
- The selected motor rotates forward and backward continuously.
- If the address is changed, the current motor stops and the new motor starts immediately.

**Bit Address Mapping:**

The script uses 4 GPIO pins as a binary input (DIP switch).
- **Bit 0 (LSB):** GPIO 18
- **Bit 1:** GPIO 19
- **Bit 2:** GPIO 20
- **Bit 3 (MSB):** GPIO 21

| Address (Binary) | Hex | Motor Selected |
| :---: | :---: | :---: |
| 0 0 0 0 | 0x0 | **Motor A** |
| 0 0 0 1 | 0x1 | **Motor B** |
| 0 0 1 0 | 0x2 | **Motor C** |
| 0 0 1 1 | 0x3 | **Motor D** |
| 0 1 0 0 | 0x4 | **Motor E** |
| 0 1 0 1 | 0x5 | **Motor F** |

*Note: 0 = OFF, 1 = ON*

---

## 4. SerialBoardTest (Serial Motor Control)

**Purpose:**
This is an interactive test utility that allows you to test individual motors via serial commands. Instead of using hardware switches or waiting for sequential tests, you simply type a letter (A-F) in the Serial Monitor to test the corresponding motor. This provides the most convenient way to debug specific motor channels during development and troubleshooting.

**Functionality:**
- Listens for serial input (characters 'A' through 'F').
- When a valid letter is received, the corresponding motor is selected and tested.
- Each motor rotates forward one full rotation, then backward one full rotation.
- After completing both directions, the test stops and waits for the next command.
- Supports both uppercase and lowercase input.

**Motor Selection:**

| Serial Input | Motor Selected |
| :---: | :---: |
| **A** or **a** | Motor A |
| **B** or **b** | Motor B |
| **C** or **c** | Motor C |
| **D** or **d** | Motor D |
| **E** or **e** | Motor E |
| **F** or **f** | Motor F |

**Usage:**
1. Flash the `SerialBoardTest.ino` sketch to the main controller board.
2. Open the Serial Monitor (set to 115200 baud).
3. Type a letter (A-F) and press Enter to test the corresponding motor.
4. Watch the serial output for test progress and completion messages.
5. Repeat with different letters to test other motors.

**Advantages:**
- No need for external hardware (DIP switches or address pins).
- Easy to use during development and debugging.
- Provides real-time feedback via serial messages.
- Can quickly switch between testing different motors without reflashing.

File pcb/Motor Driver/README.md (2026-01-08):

# Motor Driver PCB — VID6606 Breakout

This folder contains the design files, manufacturing resources, and assembly instructions for the Motor Driver PCB used in the ClockClock 24 Replica project. This board is a compact breakout for the VID6606 stepper driver IC, designed to be easily replaceable and compatible with the main Clock PCB.

---

## Folder Contents

- **KiCad Design Files:** Schematic and layout for the Motor Driver PCB.
- **Manufacturing Folder:**
  - Gerber files (ZIP) for PCB fabrication
  - [SpeedoDrive_BOM_SMD.csv](Manufacturing/SpeedoDrive_BOM_SMD.csv): Machine-readable BOM for SMD assembly

---

## Manufacturing 

1. **PCB Fabrication:**
   - The PCB was ordered from [JLCPCB](https://jlcpcb.com/)
   - Upload the Gerber ZIP file from the `Manufacturing` folder when placing your order

2. **SMD Assembly:**
    - The automatic assembly of SMD components (excluding the VID6606) was also ordered from JLCPCB.
    - During the order proces you will be prompted to upload a BOM file, to automatically populate the pcb. Use the CSV file in the `Manufacturing` folder for this purpose
    - Of course, the SMD Components can also be soldered manually if preferred.

3. **Manual Assembly:**
    - Since the VID6606 chip and the pin headers cannot be automatically assembled, these components must be soldered manually after receiving the PCB.

---

## Bill of Materials (BOM)

This BOM lists all components required to assemble one Motor Driver board.

| Quantity | Reference | Value | Footprint | Description |
|---|---|---|---|---|
| 1 | U1 | VID6606 | — | Stepper Driver IC |
| 2 | C1, C6 | 6.8 µF  | 0805 | Ceramic Capacitor |
| 2 | C2, C5 | 4.7 µF  | 0805 | Ceramic Capacitor |
| 2 | C3, C4 | 100 nF  | 0603 | Ceramic Capacitor |
| 9 | R1–R9 | 10 kΩ | 0603 | Resistor |
| 1 | J1 | Header 5P | 2.54 mm | Pin Header |
| 1 | J2 | Header 8P | 2.54 mm | Pin Header |
| 2 | J3, J4 | Header 6P | 2.54 mm | Pin Header |

---

## Images

### Soldered PCB Example
Without Pin Headers
<p align="center">
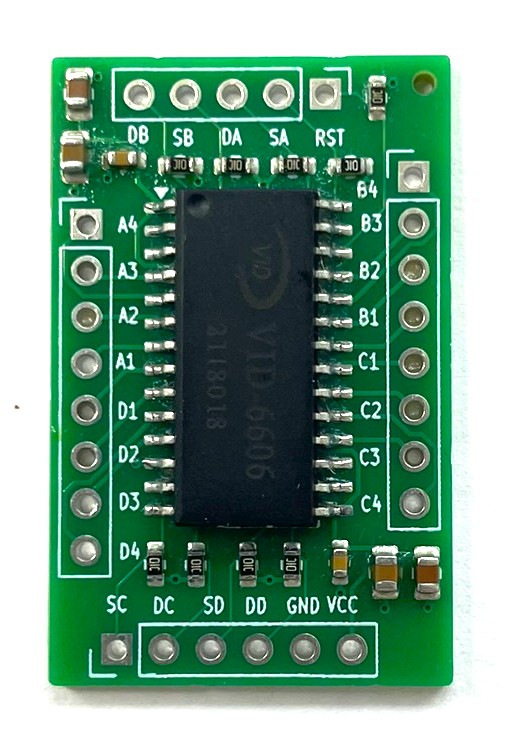
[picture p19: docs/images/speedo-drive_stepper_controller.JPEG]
Soldered Motor Driver PCB
  
  <br><em>Soldered Motor Driver PCB</em>
</p>

### PCB Schematics
<p align="center">
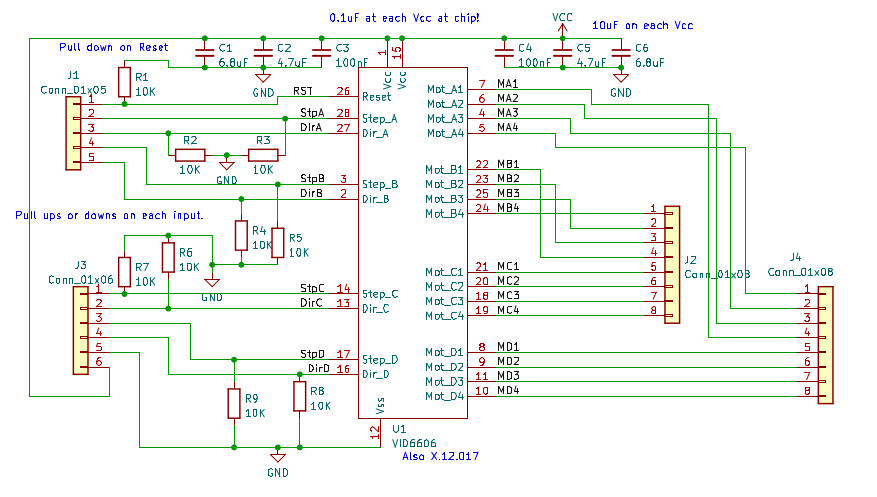
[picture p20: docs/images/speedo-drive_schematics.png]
Motor Driver Schematic
  
  <br><em>Motor Driver Schematic</em>
</p>

### Mechanical Pin Numbers
Below is an illustration of the mechanical pin numbers for the Speedo Drive PCB. This helps identify the physical pin layout and connections for assembly and troubleshooting. The pin numbering shown here was used to design the KiCad footprint for this board.

<p align="center">
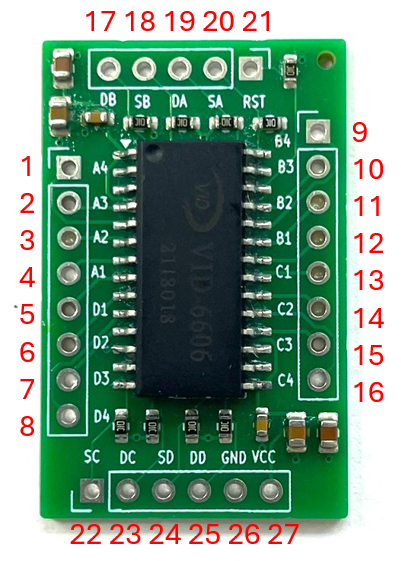
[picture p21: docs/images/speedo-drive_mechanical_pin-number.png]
Mechanical Pin Numbers
  
  <br><em>Mechanical Pin Numbers for Speedo Drive PCB</em>
</p>

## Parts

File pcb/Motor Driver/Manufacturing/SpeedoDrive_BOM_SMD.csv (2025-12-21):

Comment | Designator | Footprint | LCSC Part Number
6.8uF | C1,C6 | 0805 | C5139488
4.7uF | C2,C5 | 0805 | C1779
100nF | C3,C4 | 0603 | C14663
10K | R1,R2,R3,R4,R5,R6,R7,R8,R9 | 0603 | C25804

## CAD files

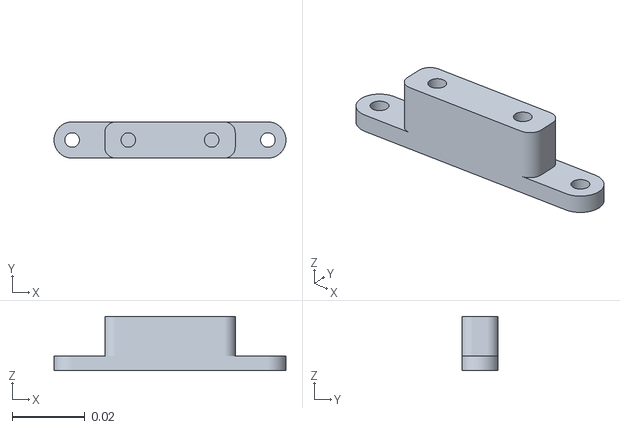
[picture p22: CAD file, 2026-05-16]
3D files/esp32_mount.stl
0.064 x 0.01 x 0.015

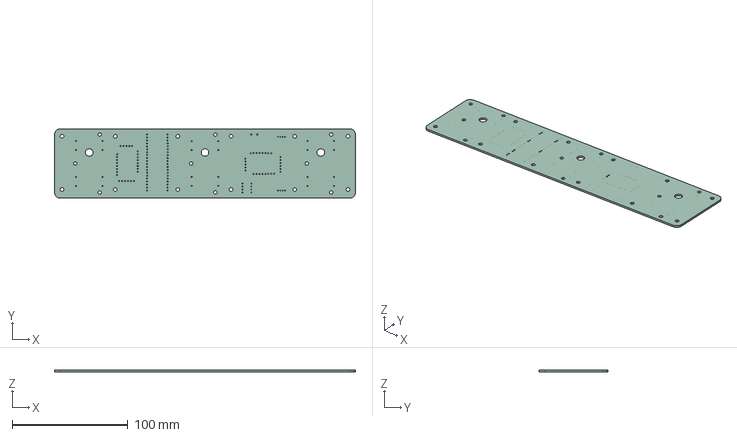
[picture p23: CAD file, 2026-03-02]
pcb/Clock PCB/3D Data/Clock_PCB.step
260.0 x 60.0 x 1.51 mm

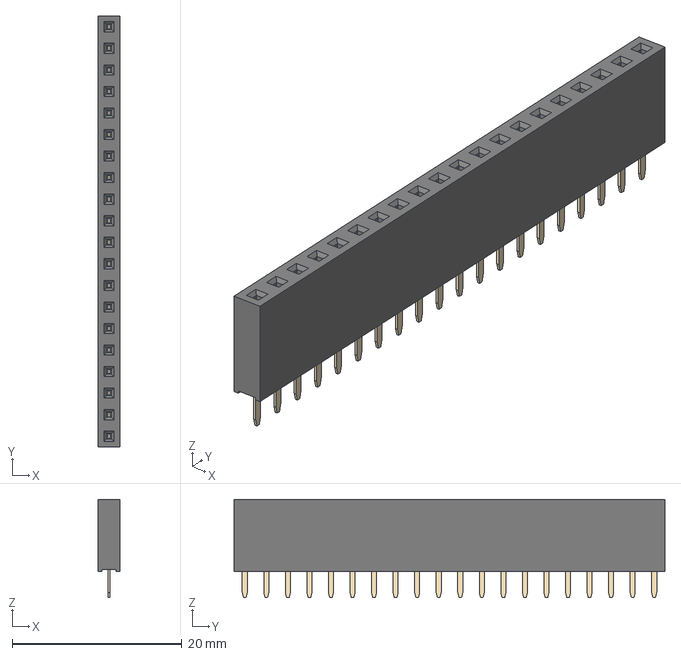
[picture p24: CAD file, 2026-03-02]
pcb/Clock PCB/3D Data/Components/PinSocket_1x20_P2.54mm_Vertical.step
2.54 x 50.8 x 11.6 mm

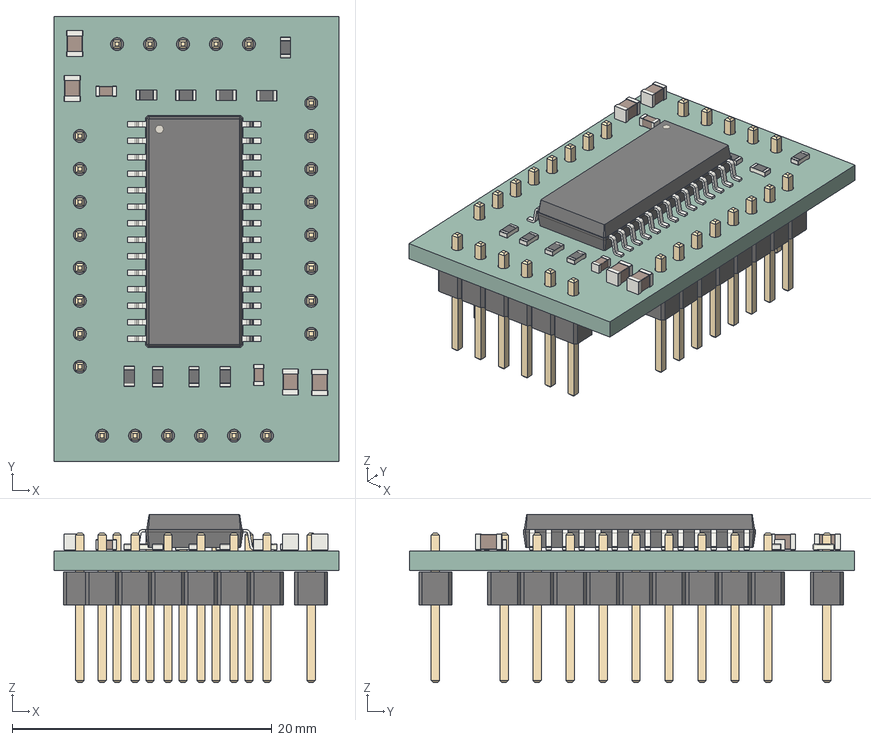
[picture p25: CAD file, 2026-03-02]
pcb/Motor Driver/3D Data/SpeedoDrive.step
22.0 x 34.3 x 13.0 mm
R_0603_1608Metric x 9
C_0805_2012Metric x 4
C_0603_1608Metric x 2
SOIC-28W_7.5x17.9mm_P1.27mm
PinHeader_1x05_P2.54mm_Vertical
PinHeader_1x08_P2.54mm_Vertical x 2
PinHeader_1x06_P2.54mm_Vertical
SpeedoDrive_PCB

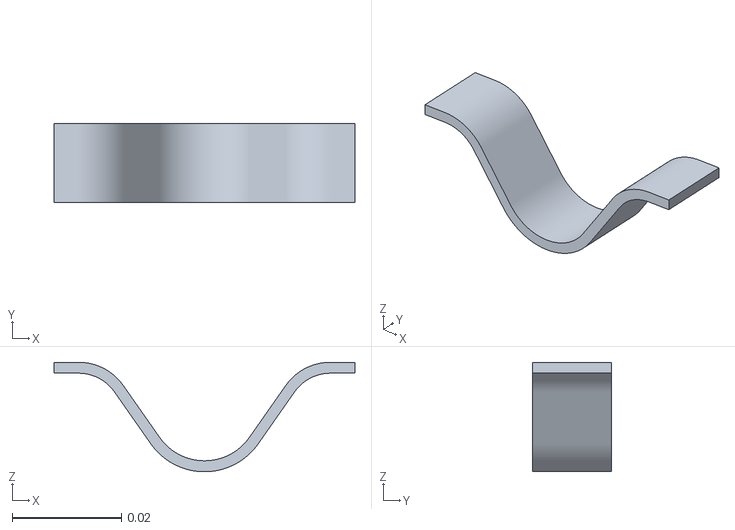
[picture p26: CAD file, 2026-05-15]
3D files/clamp_spring.stl
0.055 x 0.0145 x 0.02

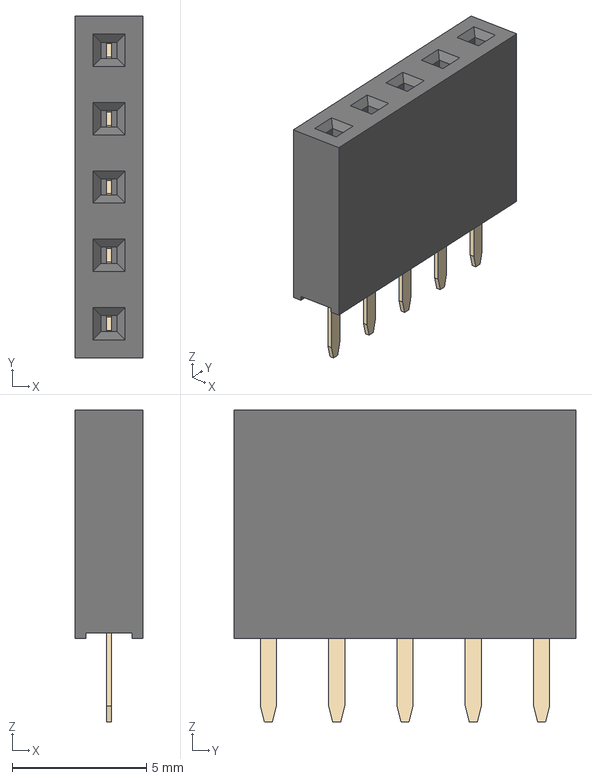
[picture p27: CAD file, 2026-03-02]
pcb/Clock PCB/3D Data/Components/PinSocket_1x05_P2.54mm_Vertical.step
2.54 x 12.7 x 11.6 mm

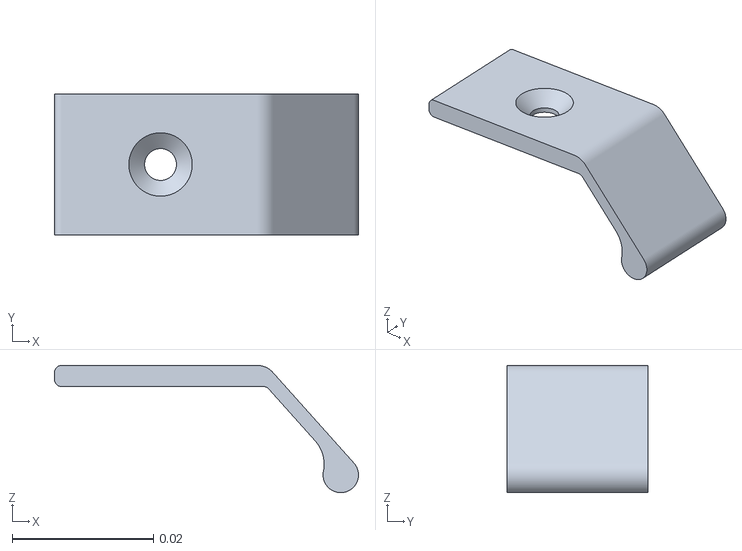
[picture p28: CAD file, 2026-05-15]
3D files/edge_clamp.stl
0.043 x 0.02 x 0.018

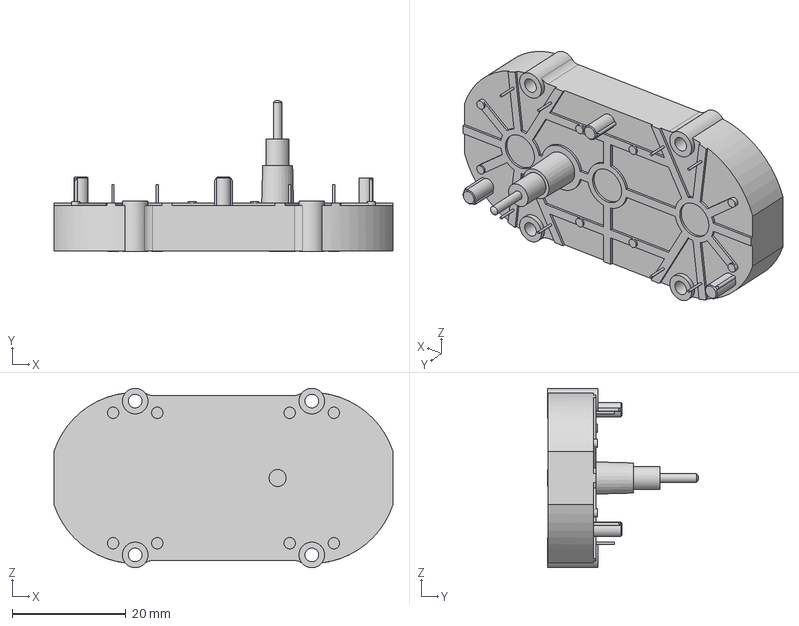
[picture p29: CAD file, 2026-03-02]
pcb/Clock PCB/3D Data/Components/BKA30D-R5.step
59.5 x 26.5 x 31.5 mm

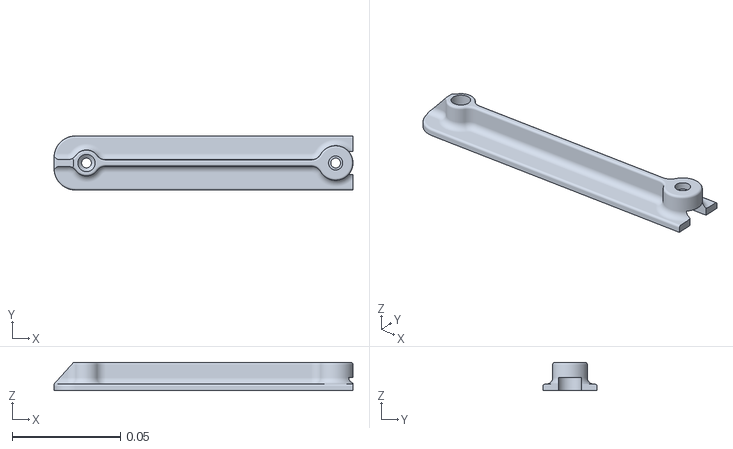
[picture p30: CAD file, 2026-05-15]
3D files/outer_clamp.stl
0.138 x 0.025 x 0.013

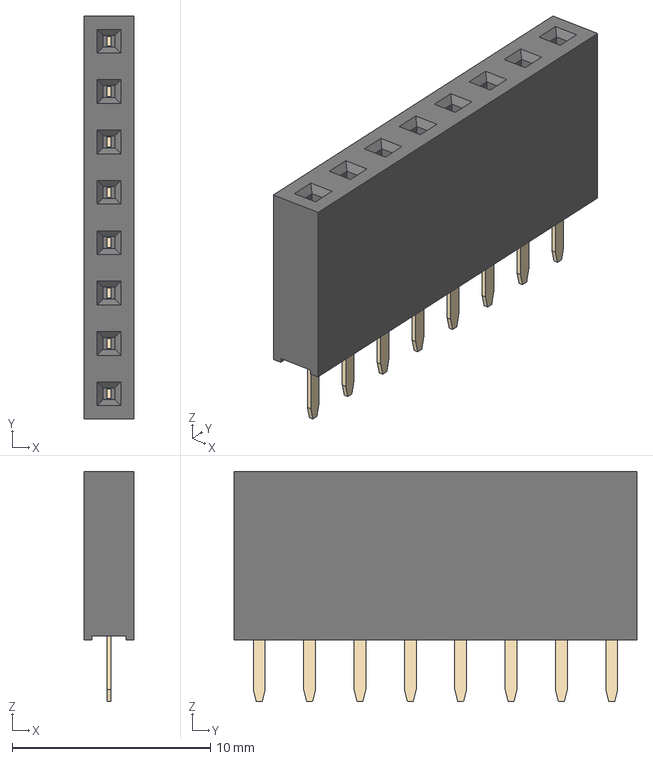
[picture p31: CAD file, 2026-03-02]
pcb/Clock PCB/3D Data/Components/PinSocket_1x08_P2.54mm_Vertical.step
2.54 x 20.3 x 11.6 mm

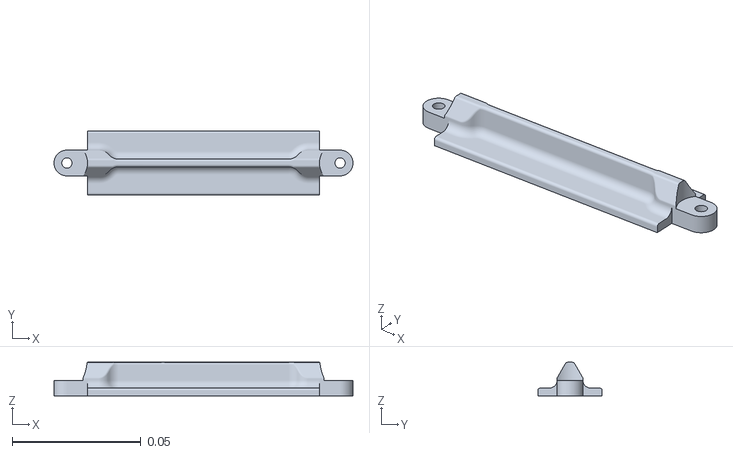
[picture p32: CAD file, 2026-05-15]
3D files/middle_clamp.stl
0.116 x 0.025 x 0.013

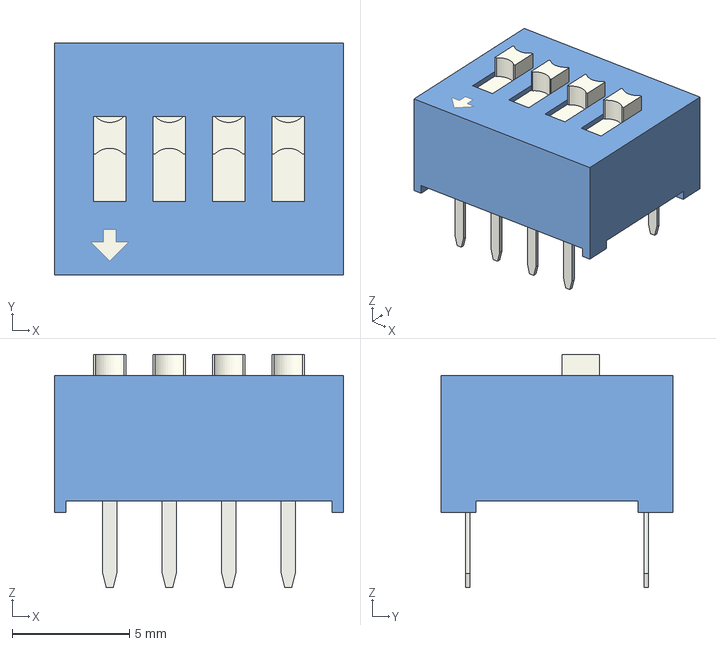
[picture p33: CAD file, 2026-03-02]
pcb/Clock PCB/3D Data/Components/SW_DIP_SPSTx04_Slide_9.78x12.34mm_W7.62mm_P2.54mm.step
12.3 x 9.90 x 9.95 mm

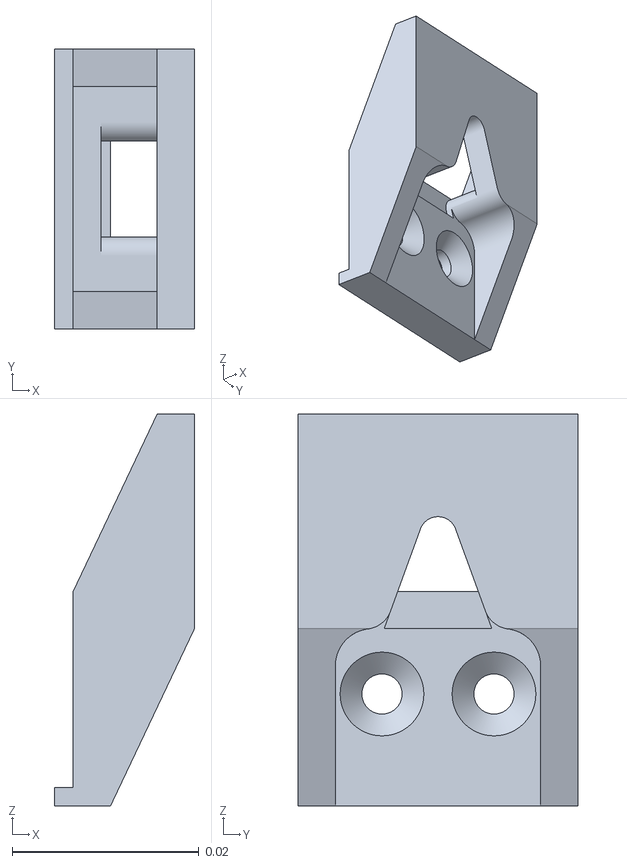
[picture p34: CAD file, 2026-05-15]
3D files/wall_mount.stl
0.015 x 0.03 x 0.042

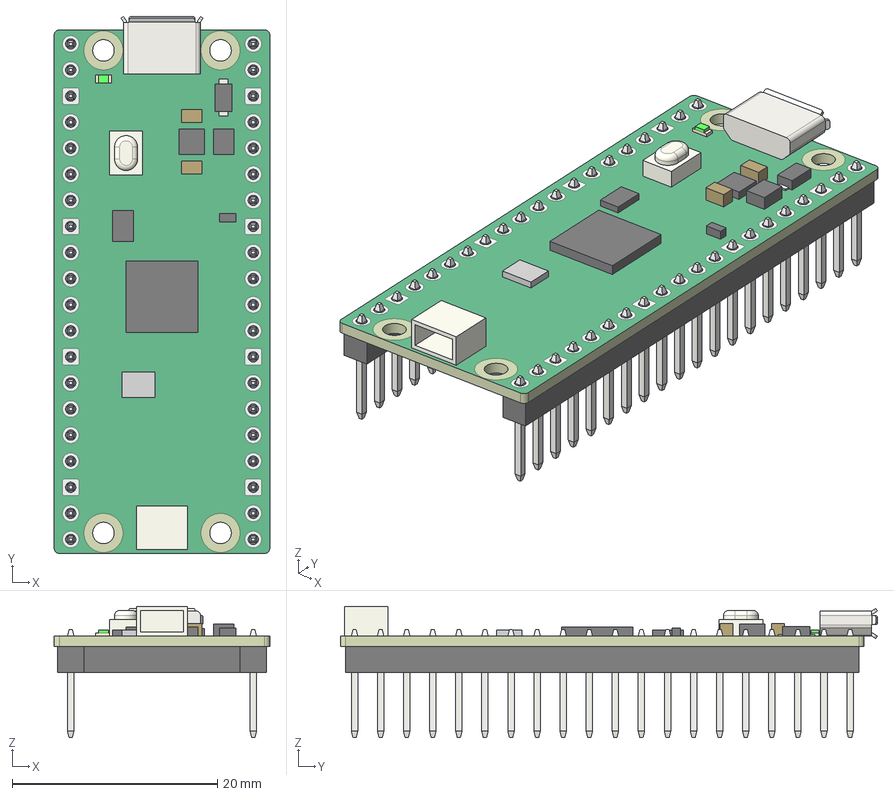
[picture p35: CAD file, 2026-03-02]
pcb/Clock PCB/3D Data/Components/RaspberryPi_Pico_H.step
21.0 x 52.3 x 12.8 mm
RaspberryPi_Pico_H_Module_KiCad
RaspberryPi_Pico_Header_DIP-40_H2.54mm_KiCad

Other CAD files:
pcb/Motor Driver/3D Data/SpeedoDrivel.stl
3D files/psu_bracket.stl
pcb/Clock PCB/3D Data/Components/PinSocket_1x06_P2.54mm_Vertical.step
3D files/mounting_aid.stl
3D files/distance_bracket.stl
3D files/lower_hand.stl
3D files/mounting_bracket.stl
3D files/pcb_mount.stl
3D files/pcb_mount_bottom.stl
3D files/screw_spacer.stl
3D files/standing_bracket.stl
3D files/upper_hand.stl
pcb/Clock PCB/3D Data/Components/JST_PH_S4B-PH-K_1x04_P2.00mm_Horizontal.step
pcb/Clock PCB/3D Data/Components/TerminalBlock_Phoenix_MKDS-1,5-2-5.08_1x02_P5.08mm_Horizontal.step

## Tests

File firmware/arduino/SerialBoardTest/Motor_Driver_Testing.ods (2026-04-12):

Driver Nr | Test M1 & M2 |  |  |  | Test M3
 | A1-A4 | B1-B4 | C1-C4 | D1-D4 | A1-A4 | B1-B4
1 | ✅ | ✅ | ✅ | ✅ | ✅ | ✅ | A is evesed direction!
2 | ✅ | ✅ | ✅ | ✅ | ✅ | ✅
3 | ✅ | ⚠ | ⚠ | ✅ | ✅ | ⚠
4 | ✅ | ✅ | ⚠ | ✅ | ✅ | ✅
5 | ✅ | ✅ | ✅ | ❌ | ✅ | ✅
6 | ✅ | ✅ | ✅ | ✅ | ✅ | ✅
7 | ✅ | ✅ | ✅ | ✅ | ✅ | ✅
8 | ❌ | ✅ | ❌ | ✅ | ❌ | ✅
9 | ✅ | ✅ | ❌ | ✅ | ✅ | ✅
10 | ✅ | ✅ | ✅ | ✅ | ✅ | ✅
11 | ✅ | ✅ | ✅ | ✅ | ✅ | ✅
12 | ✅ | ✅ | ✅ | ✅ | ✅ | ✅
13 | ⚠ | ✅ | ✅ | ✅ | ⚠ | ✅
14 | ✅ | ✅ | ✅ | ✅ | ✅ | ✅
15 | ✅ | ✅ | ❌ | ✅ | ✅ | ✅
16 | ✅ | ✅ | ✅ | ❌ | ✅ | ✅
17 | ✅ | ✅ | ✅ | ✅ | ✅ | ✅
18 | ✅ | ✅ | ✅ | ✅
19 | ✅ | ✅ | ✅ | ✅
20 | ✅ | ✅ | ✅ | ✅
21 | ✅ | ✅ | ✅ | ✅
Flawles | ✅
Works, but has noise | ⚠
Doesent work | ❌

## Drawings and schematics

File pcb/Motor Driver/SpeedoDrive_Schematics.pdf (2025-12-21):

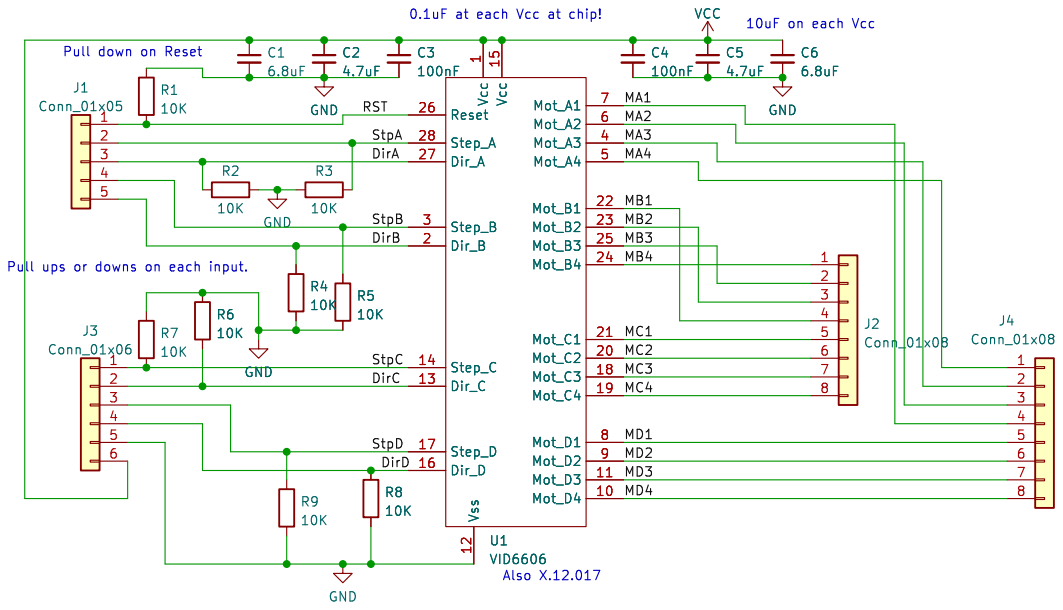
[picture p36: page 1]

Id: 1/1 Title: File: SpeedoDrive.kicad_sch Sheet: /

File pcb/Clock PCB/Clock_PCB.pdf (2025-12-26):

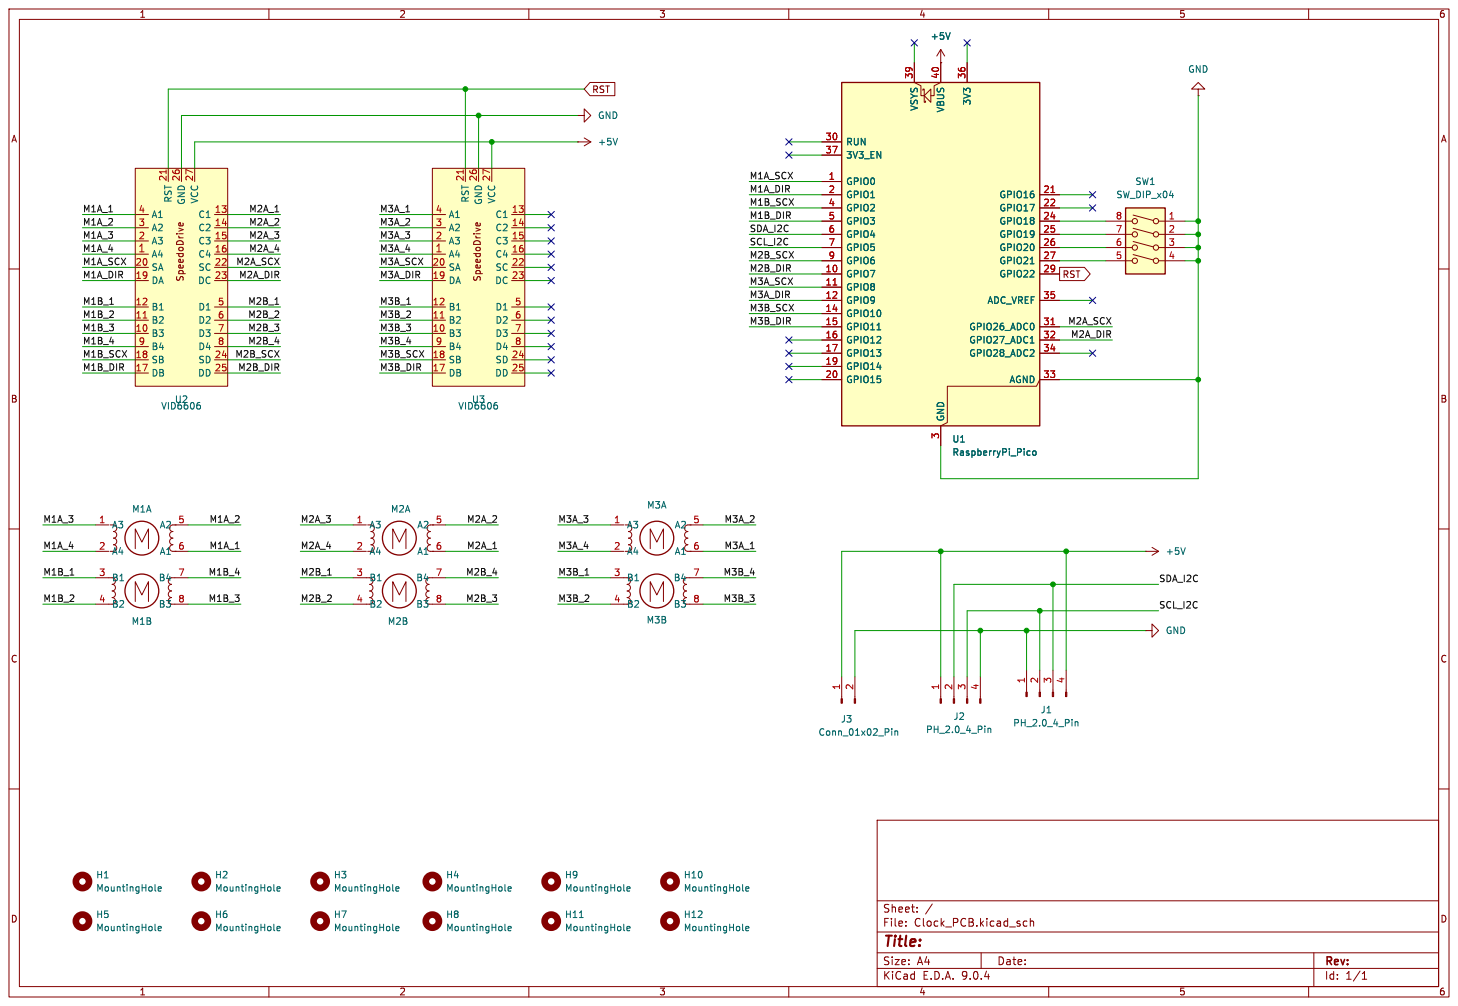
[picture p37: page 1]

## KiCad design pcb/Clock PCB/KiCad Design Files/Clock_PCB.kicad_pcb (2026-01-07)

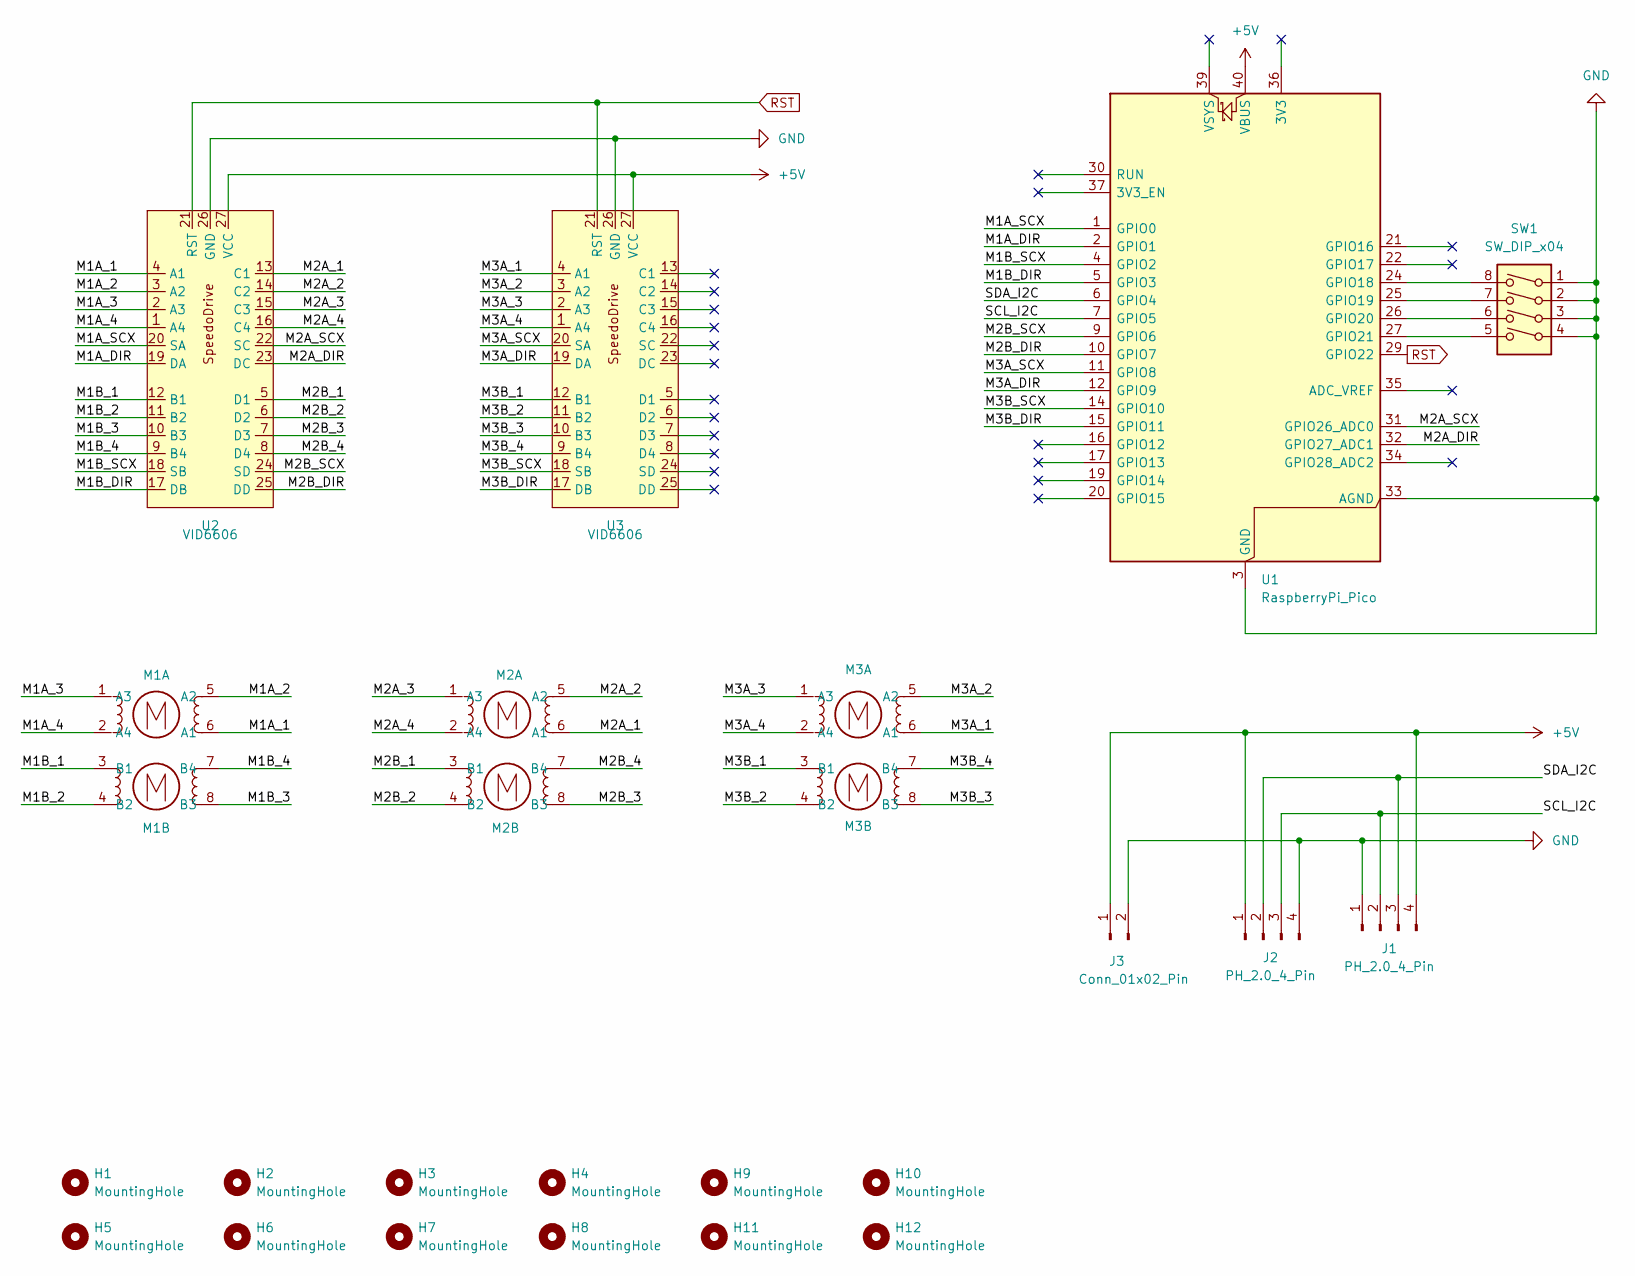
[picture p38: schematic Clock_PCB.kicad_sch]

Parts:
H1, H2, H3, H4, H5, H6, H7, H8, H9, H10, H11, H12: MountingHole; MountingHole_3.2mm_M3
J1, J2: PH_2.0_4_Pin; JST_PH_S4B-PH-K_1x04_P2.00mm_Horizontal
J3: Conn_01x02_Pin; TerminalBlock_Phoenix_MKDS-1,5-2-5.08_1x02_P5.08mm_Horizont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
M1, M2, M3: BKA30D-R5
SW1: SW_DIP_x04; SW_DIP_SPSTx04_Slide_9.78x12.34mm_W7.62mm_P2.54mm
U1: RaspberryPi_Pico; RaspberryPi_Pico_Common_THT_Header
U2, U3: VID6606; SpeedoDrive

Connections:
+5V: J1.4, J2.1, J3.1, U1.40 (VBUS), U2.27 (VCC), U3.27 (VCC)
/M1A_1: M1.6 (A1), U2.4 (A1)
/M1A_2: M1.5 (A2), U2.3 (A2)
/M1A_3: M1.1 (A3), U2.2 (A3)
/M1A_4: M1.2 (A4), U2.1 (A4)
/M1A_DIR: U1.2 (GPIO1), U2.19 (DA)
/M1A_SCX: U1.1 (GPIO0), U2.20 (SA)
/M1B_1: M1.3 (B1), U2.12 (B1)
/M1B_2: M1.4 (B2), U2.11 (B2)
/M1B_3: M1.8 (B3), U2.10 (B3)
/M1B_4: M1.7 (B4), U2.9 (B4)
/M1B_DIR: U1.5 (GPIO3), U2.17 (DB)
/M1B_SCX: U1.4 (GPIO2), U2.18 (SB)
/M2A_1: M2.6 (A1), U2.13 (C1)
/M2A_2: M2.5 (A2), U2.14 (C2)
/M2A_3: M2.1 (A3), U2.15 (C3)
/M2A_4: M2.2 (A4), U2.16 (C4)
/M2A_DIR: U1.32 (GPIO27_ADC1), U2.23 (DC)
/M2A_SCX: U1.31 (GPIO26_ADC0), U2.22 (SC)
/M2B_1: M2.3 (B1), U2.5 (D1)
/M2B_2: M2.4 (B2), U2.6 (D2)
/M2B_3: M2.8 (B3), U2.7 (D3)
/M2B_4: M2.7 (B4), U2.8 (D4)
/M2B_DIR: U1.10 (GPIO7), U2.25 (DD)
/M2B_SCX: U1.9 (GPIO6), U2.24 (SD)
/M3A_1: M3.6 (A1), U3.4 (A1)
/M3A_2: M3.5 (A2), U3.3 (A2)
/M3A_3: M3.1 (A3), U3.2 (A3)
/M3A_4: M3.2 (A4), U3.1 (A4)
/M3A_DIR: U1.12 (GPIO9), U3.19 (DA)
/M3A_SCX: U1.11 (GPIO8), U3.20 (SA)
/M3B_1: M3.3 (B1), U3.12 (B1)
/M3B_2: M3.4 (B2), U3.11 (B2)
/M3B_3: M3.8 (B3), U3.10 (B3)
/M3B_4: M3.7 (B4), U3.9 (B4)
/M3B_DIR: U1.15 (GPIO11), U3.17 (DB)
/M3B_SCX: U1.14 (GPIO10), U3.18 (SB)
/SCL_I2C: J1.2, J2.3, U1.7 (GPIO5)
/SDA_I2C: J1.3, J2.2, U1.6 (GPIO4)
GND: J1.1, J2.4, J3.2, SW1.1, SW1.2, SW1.3, SW1.4, U1.3 (GND), U1.8 (GND), U1.13 (GND), U1.18 (GND), U1.23 (GND), U1.28 (GND), U1.33 (AGND), U1.38 (GND), U2.26 (GND), U3.26 (GND)
unnamed: SW1.8, U1.24 (GPIO18)
unnamed: SW1.7, U1.25 (GPIO19)
unnamed: SW1.6, U1.26 (GPIO20)
unnamed: SW1.5, U1.27 (GPIO21)
RST: U1.29 (GPIO22), U2.21 (RST), U3.21 (RST)

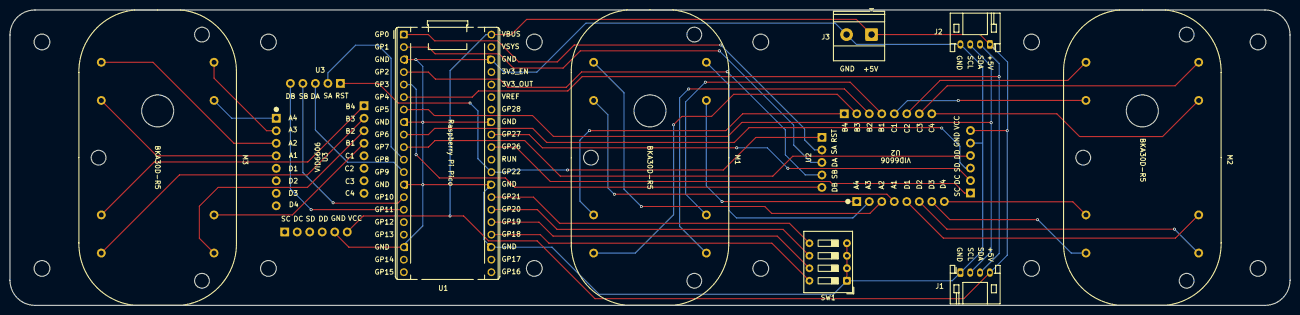
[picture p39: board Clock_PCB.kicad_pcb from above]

Board: 2 copper layers, 260.0 x 60.0 mm, 22 parts (0 on the bottom side), 45 nets.

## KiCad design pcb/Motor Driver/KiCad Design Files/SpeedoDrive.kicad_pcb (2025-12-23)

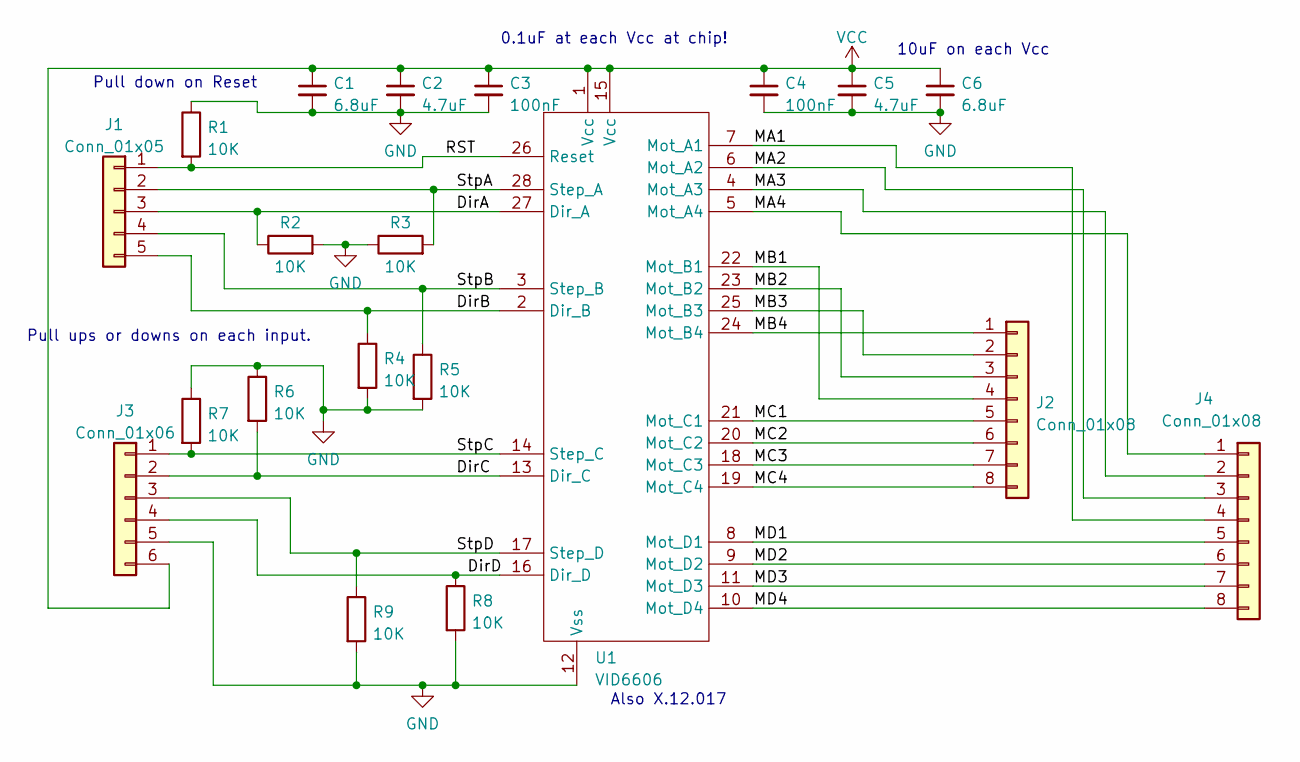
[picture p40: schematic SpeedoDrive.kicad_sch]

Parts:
C1, C6: 6.8uF; C_0805_2012MetricSQ; LCSC C5139488
C2, C5: 4.7uF; C_0805_2012MetricSQ; LCSC C1779
C3, C4: 100nF; C_0603_1608MetricSQ; LCSC C14663
J1: Conn_01x05; PinHeader_1x05_P2.54mm_Vertical
J2, J4: Conn_01x08; PinHeader_1x08_P2.54mm_Vertical
J3: Conn_01x06; PinHeader_1x06_P2.54mm_Vertical
R1, R2, R3, R4, R5, R6, R7, R8, R9: 10K; R_0603_1608MetricSQ; LCSC C25804
U1: VID6606; SOIC-28W_7.5x17.9mm_P1.27mm

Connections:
/DirA: J1.3, R2.1, U1.27 (Dir_A)
/DirB: J1.5, R4.1, U1.2 (Dir_B)
/DirC: J3.2, R6.2, U1.13 (Dir_C)
/DirD: J3.4, R8.1, U1.16 (Dir_D)
/MA1: J4.4, U1.7 (Mot_A1)
/MA2: J4.3, U1.6 (Mot_A2)
/MA3: J4.2, U1.4 (Mot_A3)
/MA4: J4.1, U1.5 (Mot_A4)
/MB1: J2.4, U1.22 (Mot_B1)
/MB2: J2.3, U1.23 (Mot_B2)
/MB3: J2.2, U1.25 (Mot_B3)
/MB4: J2.1, U1.24 (Mot_B4)
/MC1: J2.5, U1.21 (Mot_C1)
/MC2: J2.6, U1.20 (Mot_C2)
/MC3: J2.7, U1.18 (Mot_C3)
/MC4: J2.8, U1.19 (Mot_C4)
/MD1: J4.5, U1.8 (Mot_D1)
/MD2: J4.6, U1.9 (Mot_D2)
/MD3: J4.7, U1.11 (Mot_D3)
/MD4: J4.8, U1.10 (Mot_D4)
/RST: J1.1, R1.2, U1.26 (Reset)
/StpA: J1.2, R3.2, U1.28 (Step_A)
/StpB: J1.4, R5.1, U1.3 (Step_B)
/StpC: J3.1, R7.2, U1.14 (Step_C)
/StpD: J3.3, R9.1, U1.17 (Step_D)
GND: C1.2, C2.2, C3.2, C4.2, C5.2, C6.2, J3.5, R1.1, R2.2, R3.1, R4.2, R5.2, R6.1, R7.1, R8.2, R9.2, U1.12 (Vss)
VCC: C1.1, C2.1, C3.1, C4.1, C5.1, C6.1, J3.6, U1.1 (Vcc), U1.15 (Vcc)

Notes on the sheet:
0.1uF at each Vcc at chip!
Pull down on Reset
Also X.12.017
10uF on each Vcc
Pull ups or downs on each input.

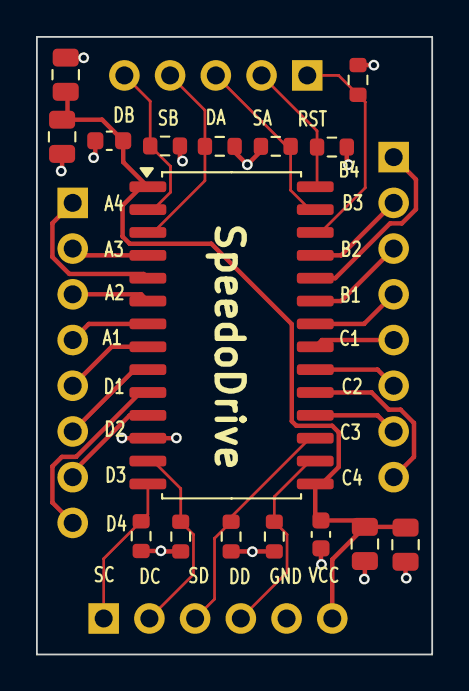
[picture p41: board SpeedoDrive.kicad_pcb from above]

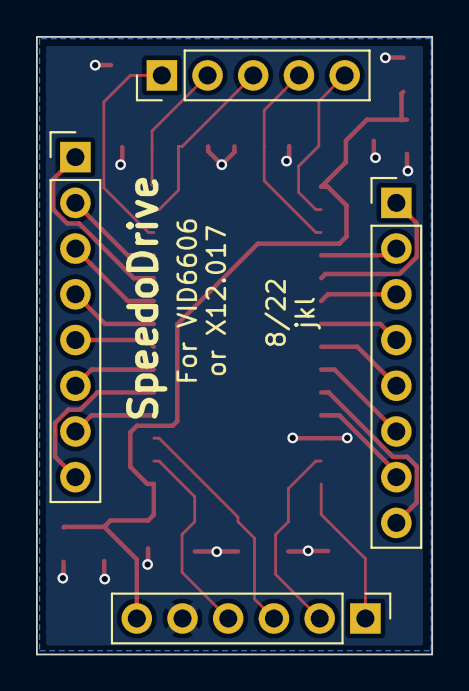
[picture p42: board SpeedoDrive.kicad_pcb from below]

Board: 2 copper layers, 22.0 x 34.3 mm, 20 parts (4 on the bottom side), 27 nets.

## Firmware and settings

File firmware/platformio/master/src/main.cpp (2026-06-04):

#include <Arduino.h>
#include <Wire.h>
#include <TimeLib.h>
#include <math.h>
#include <algorithm>

#ifndef M_PI
#define M_PI 3.14159265358979f
#endif

#include "i2c.h"
#include "clock_state.h"
#include "clock_manager.h"
#include "digit.h"
#include "wifi_utils.h"
#include "web_server.h"
#include "clock_config.h"
#include "ntp.h"


int last_hour = -1;
int last_minute = -1;
bool is_stopped = false;
int current_cycle_index = 0;

#define I2C_SCAN_INTERVAL_MS 5000
unsigned long last_i2c_scan_ms = 0;

constexpr int I2C_SDA_PIN = 21;
constexpr int I2C_SCL_PIN = 22;
constexpr uint32_t I2C_CLOCK_HZ = 100000;
constexpr uint8_t I2C_FIRST_SLAVE_ADDR = 0x08;
constexpr uint8_t I2C_LAST_SLAVE_ADDR = 0x0F;

/**
 * Sets clock to the current time
*/
void set_time();

/**
 * Dispatches to the selected animation when in ANIMATED mode
*/
void set_animated();

/**
 * Advances the cycle index and returns the next animation to play
*/
int advance_cycle();

/**
 * Sets clock time using lazy animation
*/
void set_lazy();

/**
 * Sets clock time using chaos animation
*/
void set_chaos();

/**
 * Sets clock time using waves animation
*/
void set_waves();

/**
 * Sets clock time using circle animation (synchronized spinning discs)
*/
void set_circle();

/**
 * Sets clock time using spiral animation (diagonal wave sweep)
*/
void set_spiral();

/**
 * Sets clock time using attraction animation (digits move to attraction vector field)
*/
void set_attract();

/**
 * Sets clock time using loom animation
*/
void set_loom();

/**
 * Sets clock time using star animation
*/
void set_star();

/**
 * Sets clock to stop state
*/
void stop();

/**
 * Custom delay to update web clients
 * @param value   time in milliseconds
*/
void _delay(int value);

/**
 * Scans all I2C addresses and prints found devices to Serial
*/
void i2c_scan();

/**
 * Tries to release a stuck I2C bus by clocking SCL and issuing a STOP.
 */
void i2c_recover_bus();

/**
 * Initializes I2C with explicit pins and a timeout to avoid setup lockups.
 */
void i2c_begin_safe();

void setup() {


  Serial.begin(115200);
  Serial.println("\nClockClock24 by marino222");
  delay(3000);
  // Load configuration from EEPROM
  begin_config();
  pinMode(LED_BUILTIN, OUTPUT);

  

  if(get_connection_mode() == HOTSPOT)
    wifi_create_AP("ClockClock 24", "clock");
  else if( !wifi_connect(get_ssid(), get_password(), "clock") )
  {
    set_connection_mode(HOTSPOT);
    wifi_create_AP("ClockClock 24", "clock");
  }

  if(get_connection_mode() == EXT_CONN)
  {
    // Initialize NTP
    begin_NTP();
    setSyncProvider(get_NTP_time);
    // Sync every 30 minutes
    setSyncInterval(60 * 30);
  }

  // Bring up I2C after WiFi so the device is still reachable if the bus is faulty.
  i2c_begin_safe();
  i2c_scan();

  // Starts web server
  server_start();
}

void loop() {

  update_MDNS();
  handle_webclient();

  if (is_ota_in_progress()) return;

  if(get_connection_mode() == HOTSPOT && is_time_changed_browser())
  {
    t_browser_time browser_time = get_browser_time();
    setTime(browser_time.hour, 
      browser_time.minute, 
      browser_time.second, 
      browser_time.day, 
      browser_time.month,  
      browser_time.year);
  }

  if(get_connection_mode() == EXT_CONN && get_timezone() != get_ntp_timezone())
  {
    set_ntp_timezone(get_timezone());
    setSyncProvider(get_NTP_time);
  }

  get_clock_mode() != OFF ? set_time() : stop();

  if (millis() - last_i2c_scan_ms >= I2C_SCAN_INTERVAL_MS)
  {
    last_i2c_scan_ms = millis();
    i2c_scan();
  }
}

void set_time()
{
  int day_week = (weekday() + 5) % 7;
  if(get_sleep_time(day_week, hour()))
    stop();
  else if(hour() != last_hour || minute() != last_minute)
  {
    is_stopped = false;
    last_hour = hour();
    last_minute = minute();
    switch(get_clock_mode())
    {
      case LAZY:
        set_lazy();
        break;
      case ANIMATED:
        set_animated();
        break;
    }
  }
}

void set_animated()
{
  int anim = get_clock_animation();
  if (anim == CYCLE)
    anim = advance_cycle();
  switch(anim)
  {
    case WAVE:   set_waves();  break;
    case CHAOS:    set_chaos();    break;
    case CIRCLE: set_circle(); break;
    case SPIRAL: set_spiral(); break;
    case LOOM: set_loom(); break;
    case STAR: set_star(); break;
  }
}

int advance_cycle()
{
  int anim;
  if (get_cycle_type() == RANDOM_ORDER)
  {
    uint32_t seed = (uint32_t)(hour() * 60 + minute());
    anim = (int)((seed * 2654435761UL) % 6);
  }
  else
  {
    anim = current_cycle_index;
    current_cycle_index = (current_cycle_index + 1) % 6;
  }
  return anim;
}

void set_lazy()
{
  set_speed(200);
  set_acceleration(150);
  set_direction(MIN_DISTANCE);
  set_clock_time(last_hour, last_minute);
}

void set_chaos()
{
  set_speed(400);
  set_acceleration(150);
  set_direction(CLOCKWISE2);
  set_clock_time(last_hour, last_minute);
}

/**
 * Returns the outward-ripple delay (ms) for a clock at grid position (x, y).
 * x: 1 to 8 (column), y: 1 to 3 (row).
 */
int calculate_start_delay(int x, int y, float speed_multiplier)
{
  float dx = 4.5f - x;
  float dy = 2.0f - y;
  float distance = sqrt(dx * dx + dy * dy);
  float d = speed_multiplier * (distance - 0.5f);
  return d > 0 ? (int)d : 0;
}


/**
 * @brief Calculates the dynamic offset angle (theta) for a vector pair to create an attractor field illusion.
 *
 * This function computes the required angular offset between the inward-pointing 
 * radial line (from the current grid index to the array center) and the physical 
 * unit vectors. By linearly interpolating between an inner and outer angular bound 
 * based on the Euclidean distance from the center, it generates a sweeping "V-shape" 
 * that transitions from a sharp inward pinch near the center to a wide, circular 
 * tangent near the edges of the grid.
 * * Use the bound parameters to control the shape (softness/pointiness) of the attractor field
 *
 * @param x             The horizontal index in the array grid (e.g., 1 to 8).
 * @param y             The vertical index in the array grid (e.g., 1 to 3).
 * @param inner_bound   The minimum offset angle applied at the exact center. Smaller values create a tighter V-shape.
 * @param outer_bound   The maximum offset angle applied at the maximum radius. Values near 90 degrees create a circular tangent.
 * @return float        The calculated offset angle (theta). To get the absolute angles for the physical motors, add and subtract 
 * this value from the base inward radial angle.
 */
float calculateAttractorAngle(float x, float y, float inner_bound, float outer_bound) {
  const float centerX = 4.5f;
  const float centerY = 2.0f;
  
  // Pre-calculated maximum distance from center (4.5, 2.0) to corner (1.0, 1.0)
  // sqrt((3.5 * 3.5) + (1.0 * 1.0))
  const float maxDistance = 3.64005f; 

  float dx = x - centerX;
  float dy = y - centerY;
  float distance = sqrtf(dx * dx + dy * dy);

  // Normalize distance to [0,1], clamped to prevent minor floating point over-extensions
  float t = distance / maxDistance; 
  if (t > 1.0f) t = 1.0f;

  return inner_bound + t * (outer_bound - inner_bound);
}

/**
 * @brief Calculates the absolute target angle for a specific motor in the 0 to 360 degree range.
 *
 * Computes the base inward radial angle from the specified (x, y) grid index to 
 * the center of the array. It applies the provided dynamic offset (theta) based 
 * on which motor is being calculated, and normalizes the final result to a 
 * standard Cartesian angle (0 to 360 degrees, counterclockwise from the positive x-axis).
 *
 * @param x             The horizontal index in the grid (e.g., 1 to 8).
 * @param y             The vertical index in the grid (e.g., 1 to 3).
 * @param theta         The dynamic offset angle calculated for this coordinate's V-shape.
 * @param is_hour_hand  True to calculate the hour hand (adds theta), 
 * False to calculate the minute hand (subtracts theta).
 * @return float        The absolute target angle in degrees, strictly bounded [0.0, 360.0).
 */
float calculateAbsoluteMotorAngle(float x, float y, float theta, bool is_hour_hand) {
  const float centerX = 4.5f;
  const float centerY = 2.0f;

  // atan2f uses (y, x). Multiply by 180/PI to convert to degrees.
  float base_angle = atan2f(centerY - y, centerX - x) * 57.29578f;

  float adjusted_angle = is_hour_hand ? base_angle + theta : base_angle - theta;

  // Mathematically robust normalization to strict [0, 360) range AND CW inversion
  float normalized_angle = fmodf(adjusted_angle, 360.0f);
  if (normalized_angle < 0) {
      normalized_angle += 360.0f;
  }

  // Invert CCW to CW for the physical motors
  return fmodf((360.0f - normalized_angle), 360.0f);
}

void set_circle()
{
  const int SETUP_WAIT_MS = 9000;   // ms: reach attractor field + pause
  const float DELAY_SPEED = 300.0f; // ms: per unit grid distance (ripple speed)
  const int PHASE1_SPEED = 600;     // motor speed for phase 1
  const int PHASE1_ACCEL = 150;     // motor acceleration for phase 1
  const int PHASE2_SPEED = 400;     // motor speed for phase 2
  const int PHASE2_ACCEL = 100;     // motor acceleration for phase 2
  const float INNER_BOUND = 70.0f;  // degrees: minimum angle offset at center (controls V-shape pointiness)
  const float OUTER_BOUND = 85.0f;  // degrees: maximum angle offset at edges (values near 90 create circular tangent)

  // Phase 1: All hands move to angles that form a circle pattern
  uint16_t angles_phase1[24][2]; //24 clock with each 2 hands: stores individual angles
  for (int i = 0; i < 24; i++) {
    int c = i / 3; // column (0 to 7)
    int r = i % 3; // row (0 to 2)

    // Calculate dynamic theta for this clock's position to create the attractor field illusion
    float theta = calculateAttractorAngle(c + 1, r + 1, INNER_BOUND, OUTER_BOUND);

    // Calculate distinct absolute angles for both hands
    float target_hour = calculateAbsoluteMotorAngle(c + 1.0f, r + 1.0f, theta, true);
    float target_minute = calculateAbsoluteMotorAngle(c + 1.0f, r + 1.0f, theta, false);

    // Round floats to nearest integer and cast to uint16_t
    angles_phase1[i][0] = static_cast<uint16_t>(std::round(target_minute));
    angles_phase1[i][1] = static_cast<uint16_t>(std::round(target_hour));
  }

  set_custom_clock(angles_phase1, PHASE1_SPEED, PHASE1_ACCEL, MIN_DISTANCE);
  _delay(SETUP_WAIT_MS); // Wait for setup

  // Phase 2 + 3: Ripple spin to final digits
  set_speed(PHASE2_SPEED);
  set_acceleration(PHASE2_ACCEL);

  t_full_clock final_clock = get_clock_state_from_time(last_hour, last_minute);

  // Sort the 24 clocks by delay
  struct ClockTask {
    int c; //column
    int r; //row
    int delay_ms;
  } tasks[24];

  for (int i = 0; i < 24; i++) {
    tasks[i].c = i / 3;
    tasks[i].r = i % 3;
    tasks[i].delay_ms = calculate_start_delay(tasks[i].c + 1, tasks[i].r + 1, DELAY_SPEED);
  }

  // Bubble sort tasks by delay
  for (int i = 0; i < 23; i++) {
    for (int j = 0; j < 23 - i; j++) {
      if (tasks[j].delay_ms > tasks[j+1].delay_ms) {
        ClockTask temp = tasks[j];
        tasks[j] = tasks[j+1];
        tasks[j+1] = temp;
      }
    }
  }

  unsigned long start_time = millis();
  for (int i = 0; i < 24; i++) {
    int c = tasks[i].c;
    int r = tasks[i].r;

    // Wait until it's time to trigger this clock
    while (millis() - start_time < (unsigned long)tasks[i].delay_ms) {
       update_MDNS();
       handle_webclient();
       if (is_ota_in_progress()) return;
       delay(5);
    }

    int board = c;
    int clock_idx = r;

    // Get target angle from final_clock
    int digit_idx = board / 2;
    int half_idx = board % 2;

    int target_h = final_clock.digit[digit_idx].halfs[half_idx].clocks[clock_idx].angle_h;
    int target_m = final_clock.digit[digit_idx].halfs[half_idx].clocks[clock_idx].angle_m;

    // Spin hands in opposite directions: Hour hand CW, Minute hand CCW
    set_single_clock_target_dir(board, clock_idx, target_h, target_m, CLOCKWISE2, COUNTERCLOCKWISE2);
  }
}


/**
 * Returns the angle (degrees, 0 = right, CW+) for a hand at grid
 * position (x, y) pointing toward the attractor at (cx, cy).
 */
float get_angle_to_attractor(int x, int y, float cx, float cy)
{
  return atan2(cy - y, cx - x) * 180.0f / M_PI;
}


void set_spiral()
{
  const int SETUP_WAIT_MS = 8000;   // ms: reach attractor field + pause
  const float DELAY_SPEED = 300.0f; // ms: per unit grid distance (ripple speed)
  const int PHASE1_SPEED = 500;     // motor speed for phase 1
  const int PHASE1_ACCEL = 150;     // motor acceleration for phase 1
  const int PHASE2_SPEED = 400;     // motor speed for phase 2
  const int PHASE2_ACCEL = 100;     // motor acceleration for phase 2

  // Phase 1: All hands move to attractor field (4.5, 2.0)

  uint16_t angles_phase1[24][2]; //24 clock with each 2 hands: stores individual angles
  for (int i = 0; i < 24; i++) {
    int c = i / 3; // column (0 to 7)
    int r = i % 3; // row (0 to 2)

    float angle = get_angle_to_attractor(c + 1, r + 1, 4.5f, 2.0f);

    // Ensure angle is in [0, 360) and positive
    int target = (int)round(360.0f - angle) % 360;
    if (target < 0) target += 360;
    angles_phase1[i][0] = target;
    angles_phase1[i][1] = target;
  }
  set_custom_clock(angles_phase1, PHASE1_SPEED, PHASE1_ACCEL, MIN_DISTANCE);
  _delay(SETUP_WAIT_MS); // Wait for setup

  // Phase 2 + 3: Ripple spin to final digits
  set_speed(PHASE2_SPEED);
  set_acceleration(PHASE2_ACCEL);
  set_direction(CLOCKWISE2);

  t_full_clock final_clock = get_clock_state_from_time(last_hour, last_minute);

  // Sort the 24 clocks by delay
  struct ClockTask {
    int c; //column
    int r; //row
    int delay_ms;
  } tasks[24];

  for (int i = 0; i < 24; i++) {
    tasks[i].c = i / 3;
    tasks[i].r = i % 3;
    tasks[i].delay_ms = calculate_start_delay(tasks[i].c + 1, tasks[i].r + 1, DELAY_SPEED);
  }

  // Bubble sort tasks by delay
  for (int i = 0; i < 23; i++) {
    for (int j = 0; j < 23 - i; j++) {
      if (tasks[j].delay_ms > tasks[j+1].delay_ms) {
        ClockTask temp = tasks[j];
        tasks[j] = tasks[j+1];
        tasks[j+1] = temp;
      }
    }
  }

  unsigned long start_time = millis();
  for (int i = 0; i < 24; i++) {
    int c = tasks[i].c;
    int r = tasks[i].r;

    // Wait until it's time to trigger this clock
    while (millis() - start_time < (unsigned long)tasks[i].delay_ms) {
       update_MDNS();
       handle_webclient();
       if (is_ota_in_progress()) return;
       delay(5);
    }

    int board = c;
    int clock_idx = r;

    // Get target angle from final_clock
    int digit_idx = board / 2;
    int half_idx = board % 2;

    int target_h = final_clock.digit[digit_idx].halfs[half_idx].clocks[clock_idx].angle_h;
    int target_m = final_clock.digit[digit_idx].halfs[half_idx].clocks[clock_idx].angle_m;

    set_single_clock_target(board, clock_idx, target_h, target_m);
  }
}


void set_waves()
{
  set_speed(800);
  set_acceleration(150);
  set_direction(MIN_DISTANCE);
  set_clock(d_IIII);
  _delay(9000);
  set_speed(400);
  set_acceleration(100);
  set_direction(CLOCKWISE2);
  t_full_clock clock = get_clock_state_from_time(last_hour, last_minute);
  for (int i = 0; i <8; i++)
  {
    set_half_digit(i, clock.digit[i/2].halfs[i%2]);
    delay(400);
  }
}

void stop()
{
  if(!is_stopped)
  {
    is_stopped = true;
    last_hour = -1;
    last_minute = -1;
    set_direction(MIN_DISTANCE);
    set_speed(300);
    set_acceleration(150);
    set_clock(d_stop);
  }
}

/**
 * @brief Sets clock time using the loom animation.
 * 
 * The animation begins with all clock hands aligned to form a solid horizontal block. 
 * The rows then fold outward, spinning in opposite directions (with the top and bottom rows 
 * spinning oppositely), seamlessly transitioning into the vertical digits of the current time.
 */
void set_loom()
{
  const int SETUP_WAIT_MS = 10000;
  const int PHASE1_SPEED = 600;
  const int PHASE1_ACCEL = 100;

  // Phase 1: All hands move to the loom starting position
  set_speed(PHASE1_SPEED);
  set_acceleration(PHASE1_ACCEL);
  set_direction(MIN_DISTANCE);
  set_clock(d_loom);

  _delay(SETUP_WAIT_MS);

  const int PHASE2_SPEED = 400;
  const int PHASE2_ACCEL = 100;

  // Phase 2 & 3: Spin hands in opposite directions and settle on current time
  set_speed(PHASE2_SPEED);
  set_acceleration(PHASE2_ACCEL);
  
  t_full_clock final_clock = get_clock_state_from_time(last_hour, last_minute);

  for (int i = 0; i < 24; i++) {
    int board = i / 3;
    int clock_idx = i % 3;

    int digit_idx = board / 2;
    int half_idx = board % 2;

    int target_h = final_clock.digit[digit_idx].halfs[half_idx].clocks[clock_idx].angle_h;
    int target_m = final_clock.digit[digit_idx].halfs[half_idx].clocks[clock_idx].angle_m;

    int dir_h, dir_m;
    // Bottom row spins opposite to Top and Middle rows
    if (clock_idx == 2) { 
      // Bottom row: Hour CW, Minute CCW
      dir_h = CLOCKWISE2;
      dir_m = COUNTERCLOCKWISE2;
    } else { 
      // Top and Middle rows: Hour CCW, Minute CW
      dir_h = COUNTERCLOCKWISE2;
      dir_m = CLOCKWISE2;
    }

    set_single_clock_target_dir(board, clock_idx, target_h, target_m, dir_h, dir_m);
  }
}

/**
 * @brief Sets clock time using the star animation.
 * 
 * The animation begins by moving all clock hands into a diagonal star pattern. 
 * Then, the left and right halves of each digit spin in opposite directions, 
 * smoothly transitioning the entire display into the current time.
 */
void set_star(){
  const int SETUP_WAIT_MS = 10000;
  const int PHASE1_SPEED = 600;
  const int PHASE1_ACCEL = 100;

  const int PHASE2_SPEED = 400;
  const int PHASE2_ACCEL = 100;

  // Phase 1: Move all clocks to point at center using the "star" pattern digits
  set_speed(PHASE1_SPEED);
  set_acceleration(PHASE1_ACCEL);
  set_direction(MIN_DISTANCE);
  set_clock(d_star);

  _delay(SETUP_WAIT_MS);

  // Phase 2 & 3: Spin and seamlessly settle on current time
  set_speed(PHASE2_SPEED);
  set_acceleration(PHASE2_ACCEL);

  t_full_clock final_clock = get_clock_state_from_time(last_hour, last_minute);

  for (int i = 0; i < 24; i++) {
    int board = i / 3;
    int clock_idx = i % 3;

    int digit_idx = board / 2;
    int half_idx = board % 2;

    int target_h = final_clock.digit[digit_idx].halfs[half_idx].clocks[clock_idx].angle_h;
    int target_m = final_clock.digit[digit_idx].halfs[half_idx].clocks[clock_idx].angle_m;

    int dir_h, dir_m;

    // The left half and right half spin in opposite directions
    if (half_idx == 0) { 
      // Left half: Hour CW, Minute CCW
      dir_h = CLOCKWISE3;
      dir_m = COUNTERCLOCKWISE3;
    } else { 
      // Right half: Hour CCW, Minute CW
      dir_h = COUNTERCLOCKWISE3;
      dir_m = CLOCKWISE3;
    }

    set_single_clock_target_dir(board, clock_idx, target_h, target_m, dir_h, dir_m);
  }
}

void i2c_scan()
{
  Serial.println("\n--- I2C Scanner ---");
  int found = 0;
  for (uint8_t addr = I2C_FIRST_SLAVE_ADDR; addr <= I2C_LAST_SLAVE_ADDR; addr++)
  {
    Wire.beginTransmission(addr);
    if (Wire.endTransmission() == 0)
    {
      Serial.printf("  Found device at 0x%02X (decimal %d)\n", addr, addr);
      found++;
    }
  }
  if (found == 0)
    Serial.println("  No I2C devices found!");
  Serial.printf("--- Scan done, %d device(s) found ---\n\n", found);
}

void i2c_recover_bus()
{
  pinMode(I2C_SDA_PIN, INPUT_PULLUP);
  pinMode(I2C_SCL_PIN, INPUT_PULLUP);

  const bool sda_high = digitalRead(I2C_SDA_PIN) == HIGH;
  const bool scl_high = digitalRead(I2C_SCL_PIN) == HIGH;
  if (sda_high && scl_high)
    return;

  Serial.println("[I2C] Bus busy at boot, trying recovery pulses...");

  pinMode(I2C_SCL_PIN, OUTPUT_OPEN_DRAIN);
  digitalWrite(I2C_SCL_PIN, HIGH);
  delayMicroseconds(5);

  for (int i = 0; i < 9; i++)
  {
    digitalWrite(I2C_SCL_PIN, LOW);
    delayMicroseconds(5);
    digitalWrite(I2C_SCL_PIN, HIGH);
    delayMicroseconds(5);
  }

  // STOP condition: SDA low -> SCL high -> SDA high.
  pinMode(I2C_SDA_PIN, OUTPUT_OPEN_DRAIN);
  digitalWrite(I2C_SDA_PIN, LOW);
  delayMicroseconds(5);
  digitalWrite(I2C_SCL_PIN, HIGH);
  delayMicroseconds(5);
  digitalWrite(I2C_SDA_PIN, HIGH);
  delayMicroseconds(5);

  pinMode(I2C_SDA_PIN, INPUT_PULLUP);
  pinMode(I2C_SCL_PIN, INPUT_PULLUP);
}

void i2c_begin_safe()
{
  i2c_recover_bus();
  Wire.begin(I2C_SDA_PIN, I2C_SCL_PIN, I2C_CLOCK_HZ);
  Wire.setTimeOut(25);
}

void _delay(int value)
{
  for (int i = 0; i <value/100; i++)
  {
    update_MDNS();
    handle_webclient();
    if (is_ota_in_progress()) return;
    delay(value/100);
  }
}

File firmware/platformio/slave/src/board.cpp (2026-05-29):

#include "board.h"

// Define a stepper and the pins it will use
ClockAccelStepper _motors[6] = {
  ClockAccelStepper(ClockAccelStepper::DRIVER, F_STEP, F_DIR), // 0 -> h clock 0
  ClockAccelStepper(ClockAccelStepper::DRIVER, E_STEP, E_DIR), // 1 -> m clock 0
  ClockAccelStepper(ClockAccelStepper::DRIVER, B_STEP, B_DIR), // 2 -> h clock 1
  ClockAccelStepper(ClockAccelStepper::DRIVER, A_STEP, A_DIR), // 3 -> m clock 1
  ClockAccelStepper(ClockAccelStepper::DRIVER, D_STEP, D_DIR), // 4 -> h clock 2
  ClockAccelStepper(ClockAccelStepper::DRIVER, C_STEP, C_DIR)  // 5 -> m clock 2
};

uint8_t _i2c_address = 0;

static int sanitize_angle(int angle)
{
  angle = angle % 360;
  return angle < 0 ? 360 + angle : angle;
}

void board_begin()
{
  // Reset motor controllers
  pinMode(RESET, OUTPUT);
  digitalWrite(RESET, HIGH);

  // Init motors
  for(int i = 0; i < 6; i++)
  {
    if(i % 2 == 1)
      _motors[i].setReverse(true);
    _motors[i].setMaxMotorSteps(STEPS);
    _motors[i].setHandAngle(INIT_HANDS_ANGLE);
    _motors[i].setMinPulseWidth(5);
  }

  pinMode(ADDR_1, INPUT_PULLUP);
  pinMode(ADDR_2, INPUT_PULLUP);
  pinMode(ADDR_3, INPUT_PULLUP);
  pinMode(ADDR_4, INPUT_PULLUP);
  _i2c_address = !digitalRead(ADDR_1) + 
               (!digitalRead(ADDR_2) << 1) + 
               (!digitalRead(ADDR_3) << 2) + 
               (!digitalRead(ADDR_4) << 3);
  Serial.printf("I2C address: %d (DIP: %d%d%d%d)\n", 
    _i2c_address,
    !digitalRead(ADDR_4),
    !digitalRead(ADDR_3),
    !digitalRead(ADDR_2),
    !digitalRead(ADDR_1));
}

void board_loop()
{
  for(int i = 0; i < 6; i++)
    _motors[i].run();
}

uint8_t get_i2c_address()
{
  return _i2c_address;
}

bool clock_is_running(int index)
{
  if( index < 0 || index > 2)
    return false;

  return _motors[index*2].distanceToGo() != 0 || 
         _motors[index*2 + 1].distanceToGo();
}

void set_clock(int index, t_clock state)
{
  int angle_h = sanitize_angle(state.angle_h + state.adjust_h);
  _motors[index*2].setMaxSpeed(state.speed_h);
  _motors[index*2].setAcceleration(state.accel_h);
  _motors[index*2].moveToAngle(angle_h, state.mode_h);

  int angle_m = sanitize_angle(state.angle_m + state.adjust_m);
  _motors[index*2 + 1].setMaxSpeed(state.speed_m);
  _motors[index*2 + 1].setAcceleration(state.accel_m);
  _motors[index*2 + 1].moveToAngle(angle_m, state.mode_m);
}

void adjust_h_hand(int index, signed char amount)
{
  int steps = amount * STEPS / 360;
  _motors[index*2 + 1].move(steps);
  _motors[index*2 + 1].runToPosition();
}

void adjust_m_hand(int index, signed char amount)
{
  int steps = amount * STEPS / 360;
  _motors[index*2].move(-steps);
  _motors[index*2].runToPosition();
}

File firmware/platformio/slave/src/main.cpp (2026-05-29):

#include <Wire.h>

#include "board_config.h"
#include "board.h"
#include "clock_state.h"
#include "i2c.h"
#include <WiFi.h>

const t_clock default_clock = {0, 0, 0, 0, 0, 0, 0, 0, 0, 0};

// int spin_num; //The spin lock number
spin_lock_t *spin_lock[3]; //The spinlock object that will be associated with spin_num

t_half_digit target_clocks_state;
t_half_digit current_clocks_state;

constexpr unsigned long ADDRESS_PRINT_INTERVAL_MS = 5000;
unsigned long last_address_print_ms = 0;

// I2C runs on main core (core 0)
void receiveEvent(int how_many)
{
  // Serial.println("Received something");
  if (how_many >= sizeof(half_digit))
  {
    t_half_digit tmp_state;
    I2C_readAnything (tmp_state);

    for (uint8_t i = 0; i < 3; i++)
    {
      spin_lock_unsafe_blocking(spin_lock[i]); //Acquire the spin lock without disabling interrupts
      target_clocks_state.clocks[i] = tmp_state.clocks[i];
      target_clocks_state.change_counter[i] = tmp_state.change_counter[i];
      spin_unlock_unsafe(spin_lock[i]); //Release the spin lock without re-enabling interrupts
    }
  }
}

void setup()
{  

  Serial.begin(115200);
  unsigned long serial_wait_start = millis();
  while (!Serial && millis() - serial_wait_start < 1500) delay(10);
  Serial.println("clockclock24 replica by Vallasc slave v1.0");

  delay(1000); //Wait a bit to ensure the master controller boots before the slaves

  pinMode(LED_BUILTIN, OUTPUT);
  digitalWrite(LED_BUILTIN, LOW);

  board_begin();
  target_clocks_state = {{default_clock, default_clock, default_clock}, {0, 0, 0}};

  for (uint8_t i = 0; i < 3; i++)
  {
    int spin_num = spin_lock_claim_unused(true); //Claim a free spin lock. If true the function will panic if none are available
    spin_lock[i] = spin_lock_init(spin_num); //Initialise a spin lock
  }

  Wire.setSDA(WIRE_SDA);
  Wire.setSCL(WIRE_SCL);
  Wire.begin(get_i2c_address());
  Wire.onReceive(receiveEvent);
}

void loop()
{
  if (millis() - last_address_print_ms >= ADDRESS_PRINT_INTERVAL_MS)
  {
    last_address_print_ms = millis();
    Serial.printf("[Slave] I2C address: 0x%02X (%u)\n", get_i2c_address(), get_i2c_address());
  }

  delay(10);
}

void setup1() 
{
  current_clocks_state = {{default_clock, default_clock, default_clock}, {0, 0, 0}};
}

// Steppers on core 1
void loop1()
{
  board_loop();
  for (uint8_t i = 0; i < 3; i++)
  {
    if(!clock_is_running(i) && current_clocks_state.change_counter[i] != target_clocks_state.change_counter[i])
    {
      Serial.printf("Inside clock %d\n", i);
      spin_lock_unsafe_blocking(spin_lock[i]);
      current_clocks_state.clocks[i] = target_clocks_state.clocks[i];
      current_clocks_state.change_counter[i] = target_clocks_state.change_counter[i];
      spin_unlock_unsafe(spin_lock[i]);

      if(current_clocks_state.clocks[i].mode_h == ADJUST_HAND)
        adjust_h_hand(i, current_clocks_state.clocks[i].adjust_h);

      if(current_clocks_state.clocks[i].mode_m == ADJUST_HAND)
        adjust_m_hand(i, current_clocks_state.clocks[i].adjust_m);

      if(current_clocks_state.clocks[i].mode_h <= MAX_DISTANCE3)
        set_clock(i, current_clocks_state.clocks[i]);
    }
  }
}

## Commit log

2025-12-20 Add README files for firmware and PCB design documentation
2025-12-20 Enhance firmware documentation and add Arduino test scripts for motor control
2025-12-20 Changed pcb\README
2025-12-21 Add .gitignore to exclude KiCad project files
2025-12-21 Added KiCad Design Files for Motor Driver
    [SpeedoDrive.kicad_pcb, SpeedoDrive.kicad_sch]
2025-12-21 Add STL files for clockclock24 lower and upper hands
    [clockclock24 lower hand.stl, clockclock24 upper hand.stl]
2025-12-21 Add BKA30D-xx stepper motor datasheet PDF
2025-12-21 Add README for Motor Driver PCB with manufacturing instructions and images
2025-12-21 Add BOM and Gerber files for SpeedoDrive Motor Driver
    [SpeedoDrive_BOM_SMD.csv]
2025-12-21 Added schematics, and 3D-Model for Motor Controller PCB
    [SpeedoDrive_3D-Model.stl]
2025-12-21 Replaced STl with STEP
    [SpeedoDrive_3D-Model.step, SpeedoDrive_3D-Model.stl]
2025-12-21 Revert "Replaced STl with STEP"
    This reverts commit a0bf36969092759c93fa24be8c9574c88c82bfb0.
    [SpeedoDrive_3D-Model.step, SpeedoDrive_3D-Model.stl]
2025-12-21 Update README to include PCB schematics image
2025-12-21 Refine README for PCB design files: enhance clarity and consistency in descriptions
2025-12-21 Update README files for firmware and Arduino scripts
2025-12-21 Improve comments in BoardTest.ino
2025-12-21 Add AdvancedBoardTest for stepper motor control using DIP address
2025-12-21 Add AdvancedBoardTest for testing stepper motors with DIP addressing
2025-12-21 Remove obsolete test scripts for stepper motor control
2025-12-21 Refactor SpeedoDriveTest for VID6606 compatibility and improve motor control logic
2025-12-22 Add VID6606 datasheet PDF for stepper motor driver
2025-12-23 Added datasheet for Raspberry Pi Pico
2025-12-23 Add new images for BKA30D, ESP32, motor driver, and Raspberry Pi Pico
2025-12-23 Changes on kicad files for Motor Driver
    [SpeedoDrive.kicad_pcb]
2025-12-23 Enhance README.md with detailed descriptions and images for BKA30D-R5 motors, VID6606 motor drivers, and power supply specifications
2025-12-23 Added KiCad design files for Clock PCB
    [Clock_PCB.kicad_pcb, Clock_PCB.kicad_sch]
2025-12-24 Add mechanical pin number illustration to Motor Driver README.md
2025-12-24 Clock PCB development
    [Clock_PCB.kicad_pcb, Clock_PCB.kicad_sch]
2025-12-25 KiCad PCB changes - PCB now finished, Design Review pending
    [Clock_PCB.kicad_pcb, Clock_PCB.kicad_sch]
2025-12-25 Added PCB schematics and 3d model
2025-12-25 Moved KiCad Files into folder
    [Clock_PCB.kicad_pcb, Clock_PCB.kicad_sch]
2025-12-26 Changes on Clock PCB
    [Clock_PCB.kicad_pcb]
2025-12-26 Added Gerber Files for testing (not final)
2025-12-26 Update Clock PCB
    [Clock_PCB.kicad_pcb, Clock_PCB.kicad_sch]
2025-12-31 Update motor driver capacity in README
    Corrected the number of motors that can be driven by one VID6606 motor driver from two to four.
2026-01-07 Added rendered image of Clock PCB
    [Clock_PCB.kicad_pcb]
2026-02-14 Fixed the GPIO matching
    [BoardTest.ino]
2026-02-22 Added: - API endpoints for testing - http test script - Arduino SerialBoardTest script - documentation
2026-02-26 Moved arduino file
2026-02-28 Added new arduino testing script Documented motor driver test
    [Motor_Driver_Testing.ods]
2026-02-28 Clarified I2C address numbering in README.md
2026-02-28 Coorected pin numbers in board_config.h
2026-02-28 Switched motors a & b with c & d
2026-03-02 Added and moved 3d files
    [BKA30D-R5.step, Clock_PCB.step, JST_PH_S4B-PH-K_1x04_P2.00mm_Horizontal.step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]
2026-03-22 Add I2C scanning functionality and update pin configurations in firmware
    [Motor_Driver_Testing.ods]
2026-04-12 Major update
    [clockclock24 lower hand.stl, clockclock24 upper hand.stl, distance_bracket.stl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]
2026-05-15 Added description about gap clamps Added new 3d files Added new images
    [clamp_spring.stl, edge_clamp.stl, middle_clamp.stl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]
2026-05-16 Added esp32_mount
    [esp32_mount.stl]
2026-05-29 Fixed I2C communication issues
    [board.cpp, clock_manger.cpp, main.cpp]
2026-05-31 Implemented circle animation Added button to test animation
2026-05-31 Refactor clock management and enhance web assets
    - Removed debug print statements in clock manager for cleaner code.
    - Added new functions for calculating angles in a circular layout for clock hands.
    - Implemented a new set_circle function to manage clock animations in three phases.
    - Updated web minimization script to inline CSS and JS files for better performance.
    - Adjusted attractor path in script.js to align with new clock grid dimensions.
2026-06-01 Implemented attract animation, however it is currently unstable
    [main.cpp]
2026-06-04 - Implemented Star animation - removed attract animation as it was unstable
    [main.cpp]

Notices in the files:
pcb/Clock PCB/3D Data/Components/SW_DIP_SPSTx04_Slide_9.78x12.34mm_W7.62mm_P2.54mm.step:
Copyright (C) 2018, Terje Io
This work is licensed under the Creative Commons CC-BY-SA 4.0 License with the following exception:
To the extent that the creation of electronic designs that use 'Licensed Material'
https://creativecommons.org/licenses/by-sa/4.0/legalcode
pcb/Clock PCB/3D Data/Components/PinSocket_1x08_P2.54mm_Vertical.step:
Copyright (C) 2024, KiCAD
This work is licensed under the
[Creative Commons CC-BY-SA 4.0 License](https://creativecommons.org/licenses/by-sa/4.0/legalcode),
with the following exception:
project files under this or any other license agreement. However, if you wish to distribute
